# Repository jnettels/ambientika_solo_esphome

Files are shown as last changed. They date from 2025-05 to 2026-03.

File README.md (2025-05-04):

# Ambientika Solo+ ESPHome
ESPHome Setup for Home Assistant that allows local control of a "Südwind Ambientika Solo+" ventilation system. Replaces the default infrared remote control with an ESP32 microcontroler for controlling all the ventilator functions via WLAN from Home Assistant.

This solution is heavily inspired by https://github.com/Cicatr1x/Ambientika-ESP32-Control

There is a "smart" version of this product for 619€ instead of 379€ which you can integrate into Home Assistant via a cloud connection and this integration:
https://github.com/ambientika/HomeAssistant-integration-for-Ambientika.
But with some soldering and programming, we can achieve a much cheaper and fully local control.

## Components
- **Ambientika solo+**
	- The fan that we will make Home Assistant-compatible.
	- Provides 24V and GND for our custom modules.
	- https://www.ambientika.eu/dezentrale-wohnraumlueftung-ambientika-solo-einzelraumloesung-neu/sw10038
-   **ESP32 D1 Mini**
	- The microcontroller used to control the other components.
	- https://www.amazon.de/dp/B0DHY6WXV5
-   **MP1584EN DC-DC 3A Step-Down Converter**: 
	- Converter used to step down the available 24V to 5V for the ESP32.
	- https://www.amazon.de/dp/B07DJ5HZ7G
- **GP8403 2-Channel I2C DAC Module (0-10V)**
	- This module can output a voltage between 0-10V and is connected to the ESP32 via the I2C interface.
	- The voltage controls the speed of the fan.
	- https://www.komputer.de/zen/index.php?main_page=product_info&products_id=654
	- https://www.dfrobot.com/product-2613.html
- **5V Relais Module**
	- This relay controls the 230V voltage to the component responsible for opening the ventilation cover.
	- https://www.komputer.de/zen/index.php?main_page=product_info&products_id=707

## Setup
The original is controled via infrared-remote and provides three speed settings. The voltages were measured on the original configuration and implemented here.

The onboard 24V DC needs to be converted to 5V DC (with a MP1584EN) to power a ESP-32. It controls a GP8403 via I2C, which outputs any voltage between 0V and 10V.
The ESP-32 also controls a relay module, which in turn controls the 230V deliverd to the "100331.14" actuator, which keeps the ventilation flap/cover open during operation.

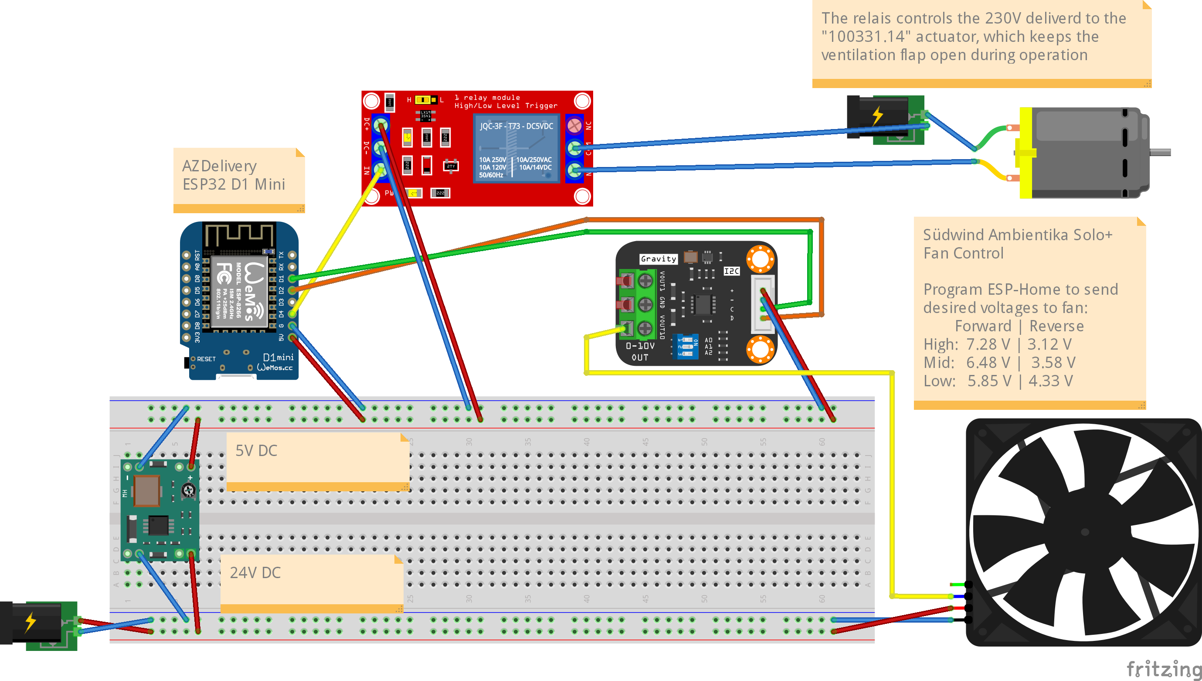
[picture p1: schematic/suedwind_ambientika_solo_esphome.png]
Schematic


The states of the fan and cover are synchronized in the automations, such that the cover is always open when the fan is active. When direction is changed, a 10 second pause is implemented to allow the fan to stop spinning, before turning it in the other direction. The oscillating mode copies the original, which changes directions after 70 seconds.

The esp32 boards needs to be loaded with the ESPHome yaml configuration provided in the config folder. This will create a ``Fan`` entity in Home Assistant. There a many tutorials for installing ESPHome.

The directions are defined as follows:
- forward = outward
- reverse = inward

## Installation
The original setup with the infrared board. It connects to 230V, 24V and to the fan motor. We will reuse those connections.
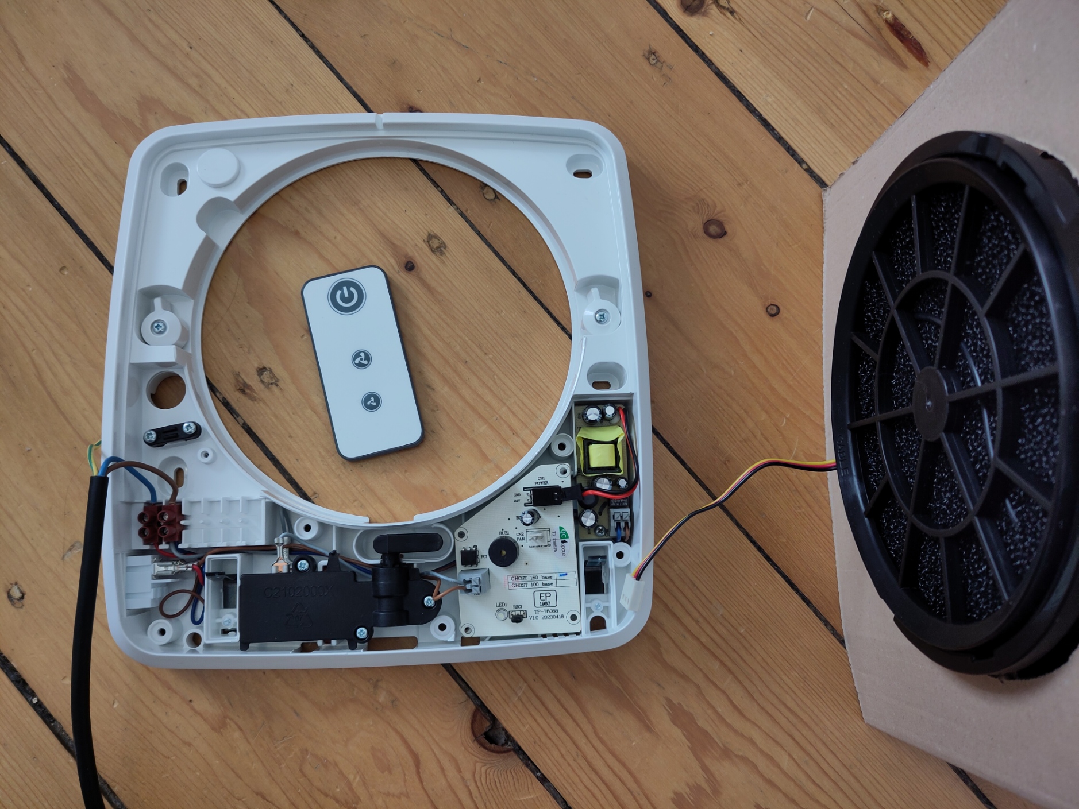
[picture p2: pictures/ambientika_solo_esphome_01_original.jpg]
Original


The custom components fully connected look like this:
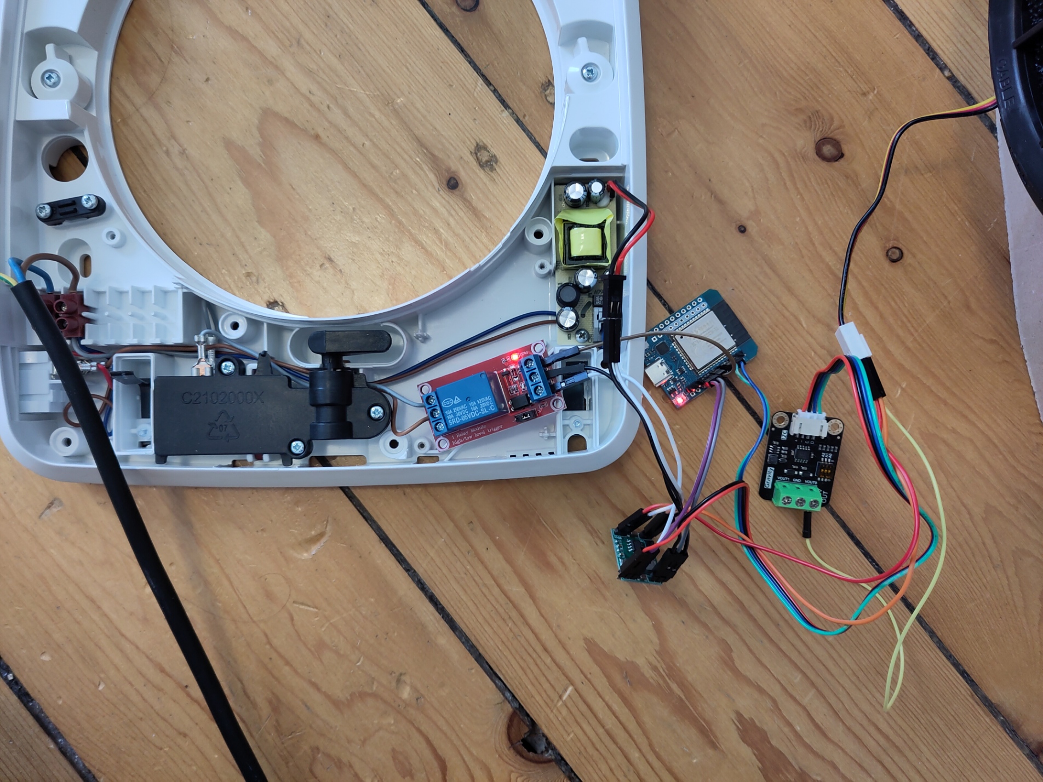
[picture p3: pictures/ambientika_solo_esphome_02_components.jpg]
Components


The final setup with all components within the fan casing. This did not seem possible and took me a lot of time, but worked out in the end. I had to cut the interior plastic away at some spots.
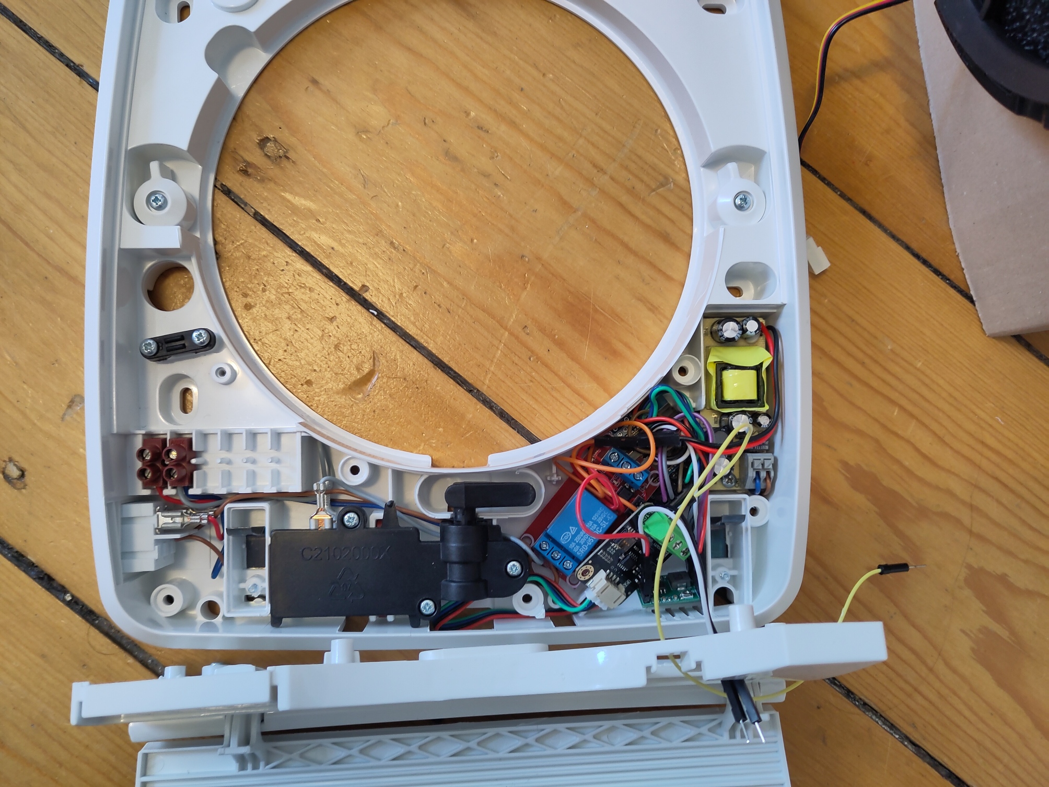
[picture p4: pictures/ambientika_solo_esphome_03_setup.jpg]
Setup


The housing can be closed, as usual:
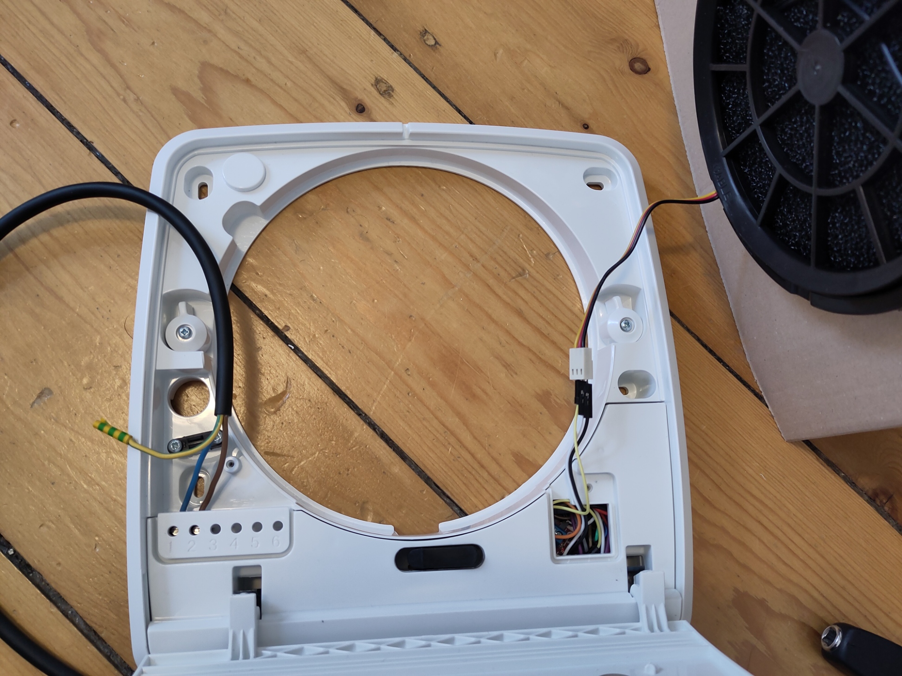
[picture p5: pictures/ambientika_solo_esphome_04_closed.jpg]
Closed


As you can see, the ventilation cover is held open by the enabled system. The infrared remote control is no longer needed :-)
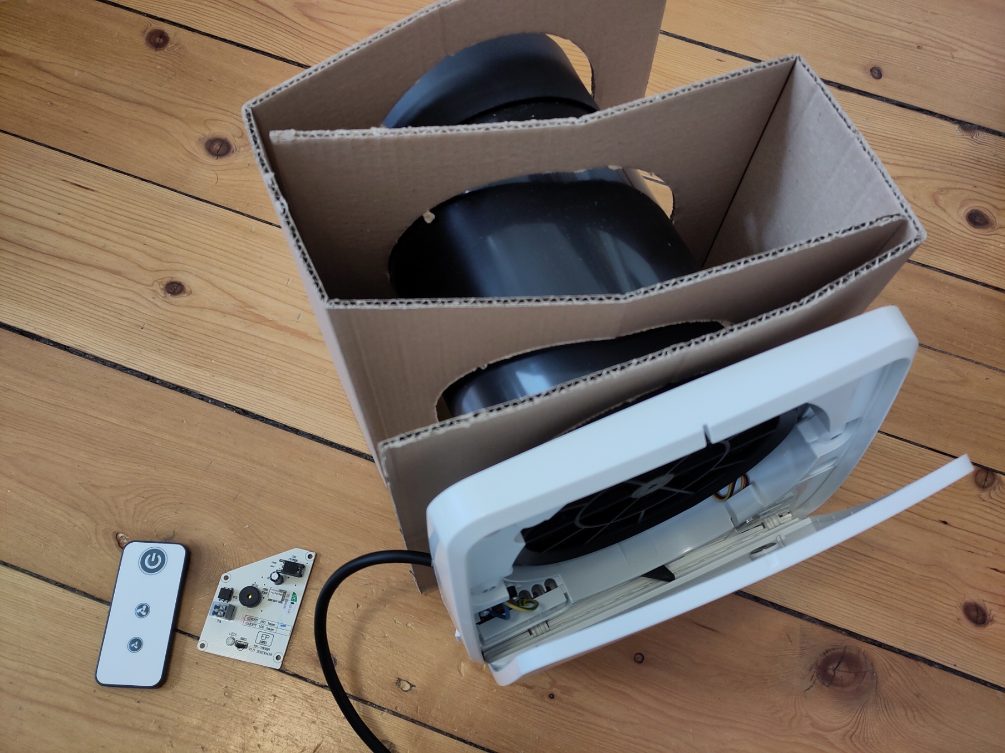
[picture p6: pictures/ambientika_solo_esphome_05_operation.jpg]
Operation


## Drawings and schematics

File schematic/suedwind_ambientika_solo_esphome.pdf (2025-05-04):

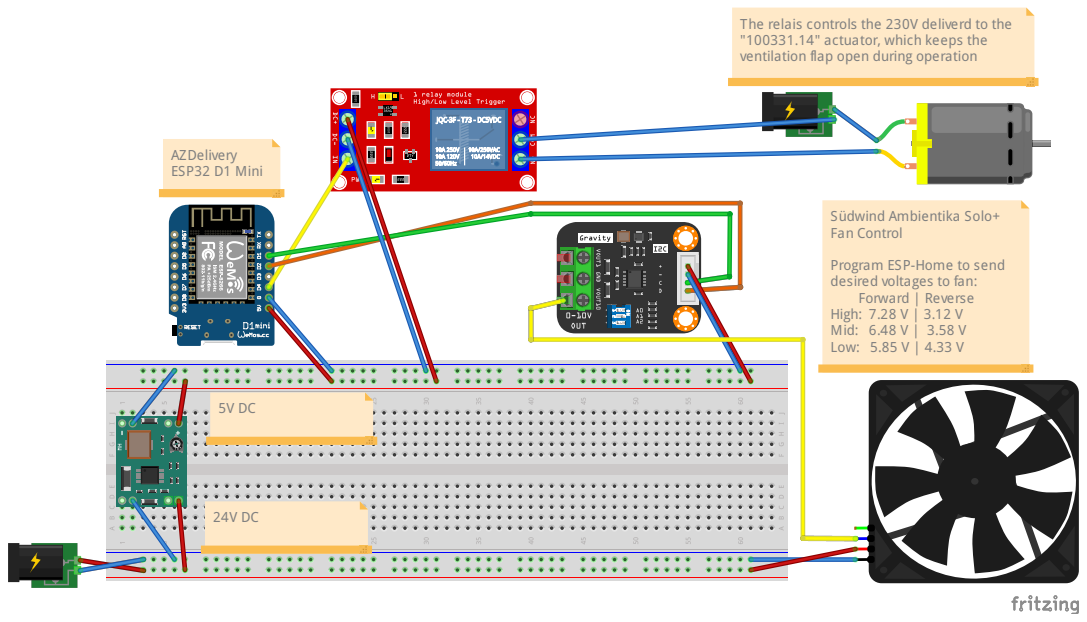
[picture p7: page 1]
AZDelivery ESP32 D1 Mini

The relais controls the 230V deliverd to the
"100331.14" actuator, which keeps the
ventilation flap open during operation

Südwind Ambientika Solo+
Fan Control

Program ESP-Home to send
desired voltages to fan:
Forward | Reverse
High: 7.28 V | 3.12 V
Mid: 6.48 V | 3.58 V
Low: 5.85 V | 4.33 V

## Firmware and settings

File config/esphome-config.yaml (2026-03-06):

# Fan control for "Südwind Ambientika Solo+"

# https://www.ambientika.eu/dezentrale-wohnraumlueftung-ambientika-solo-einzelraumloesung-neu/sw10038

# The original is controled via infrared-remote and provides three speed settings.
# The voltages were measured on the original configuration and implemented here.

# Setup:
# The onboard 24V DC needs to be converted to 5V DC (with a MP1584EN) to power a ESP-32.
# It controls a GP8403 via I2C, which outputs any voltage between 0V and 10V.
# (An input signal between 0...1 results in the output range of 0V...10V.)
# The ESP-32 also controls a relay module, which in turn controls the 230V
# delivered to the "100331.14" actuator, which keeps the ventilation flap/cover open
# during operation.

# The states of the fan and cover are synchronized in the automations below, such
# that the cover is always open when the fan is active.
# When direction is changed, a 10 second pause is implemented to allow the fan
# to stop spinning, before turning it in the other direction.

# The oscillating mode copies the original, which changes directions after 70 seconds.

# The directions are defined as follows
# forward: outward
# reverse: inward

esphome:
  name: esphome-web-4c1848
  friendly_name: Ventilation Controller
  min_version: 2024.11.0
  name_add_mac_suffix: false
  on_boot:
    - priority: 900
      then:
        - output.set_level:
            id: my_gp8403_output_1
            level: 0
        - fan.turn_off: my_fan
        - lambda: |-
            id(fan_voltage).publish_state(0);
        - component.update: fan_direction

esp32:
  board: esp32dev
  framework:
    type: esp-idf

# Enable logging
logger:

# Enable Home Assistant API
api:

# Allow Over-The-Air updates
ota:
- platform: esphome

wifi:
  ssid: !secret wifi_ssid
  password: !secret wifi_password

i2c:
  sda: 21
  scl: 22
  scan: true
  frequency: 400kHz
  id: bus_a

gp8403:
  id: my_gp8403
  voltage: 10V
  address: 0x5F

output:
  - platform: gp8403
    id: my_gp8403_output_1
    gp8403_id: my_gp8403
    channel: 0
  - platform: gp8403
    id: my_gp8403_output_2
    gp8403_id: my_gp8403
    channel: 1

switch:
  - platform: gpio
    id: cover_relay
    name: "Lüfterklappe"
    pin: 16
    # internal: true

sensor:
  - platform: template
    id: fan_voltage
    name: "Spannung Lüfter"
    device_class: voltage
    unit_of_measurement: V
    entity_category: "diagnostic"
    filters:
      - multiply: 10

text_sensor:
  - platform: template
    id: fan_direction
    name: "Richtung"
    icon: mdi:arrow-oscillating
    entity_category: "diagnostic"
    update_interval: never
    lambda: |-
        if (id(my_fan).direction == FanDirection::FORWARD) {
          return {"Vorwärts"};
        } else if (id(my_fan).direction == FanDirection::REVERSE) {
          return {"Rückwärts"};
        } else {
          return {"Unbekannt"};
        }

script:
  - id: apply_fan_output
    then:
      - lambda: |-
          // The variable v takes values between 0...1 and
          // results in voltages of 0V...10V by the GP8403 module.
          float v = 0.0;

          if (!id(my_fan).state || id(my_fan).speed == 0) {
            v = 0.0;
          } else if (id(my_fan).direction == FanDirection::FORWARD) {
            // Fan direction is forward (outward)
            if (id(my_fan).speed == 3) v = 0.312;
            else if (id(my_fan).speed == 2) v = 0.358;
            else if (id(my_fan).speed == 1) v = 0.433;
          } else {
            // Fan direction is reverse (inward)
            if (id(my_fan).speed == 3) v = 0.728;
            else if (id(my_fan).speed == 2) v = 0.648;
            else if (id(my_fan).speed == 1) v = 0.585;
          }

          id(my_gp8403_output_1).set_level(v);
          id(fan_voltage).publish_state(v);

          if (v > 0.001) {
            if (!id(cover_relay).state) id(cover_relay).turn_on();
          } else {
            if (id(cover_relay).state) id(cover_relay).turn_off();
          }
  - id: run_fan_oscillation
    mode: restart
    then:
      - while:
          condition:
            lambda: return id(my_fan).state && id(my_fan).oscillating;
          then:
            - delay: 70s
            - lambda: |-
                if (!id(my_fan).state) return;
                auto call = id(my_fan).make_call();
                call.set_direction(
                  id(my_fan).direction == FanDirection::FORWARD
                    ? FanDirection::REVERSE
                    : FanDirection::FORWARD
                );
                call.perform();
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
